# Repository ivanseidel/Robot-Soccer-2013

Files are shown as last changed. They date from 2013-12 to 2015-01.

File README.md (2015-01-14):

Soccer-Robot-2013
=================

RoboCup Junior Soccer

This repository was created to share the entire RoboCup Junior Soccer robot project,
including Rendering, SolidWorks CAD drawings, simulations, software code and libraries.

The project was developed by team EmeroCHS (Emerotecos with CHS)  from Brazil, for the national and international
RoboCup at Eidhoven.

At the same time, we were developing a Soccer B robot for RoboCup too. They both use almost the same electronics design and concept. Here is the [Rescue B project repository](https://github.com/ivanseidel/Robot-Rescue-2013).

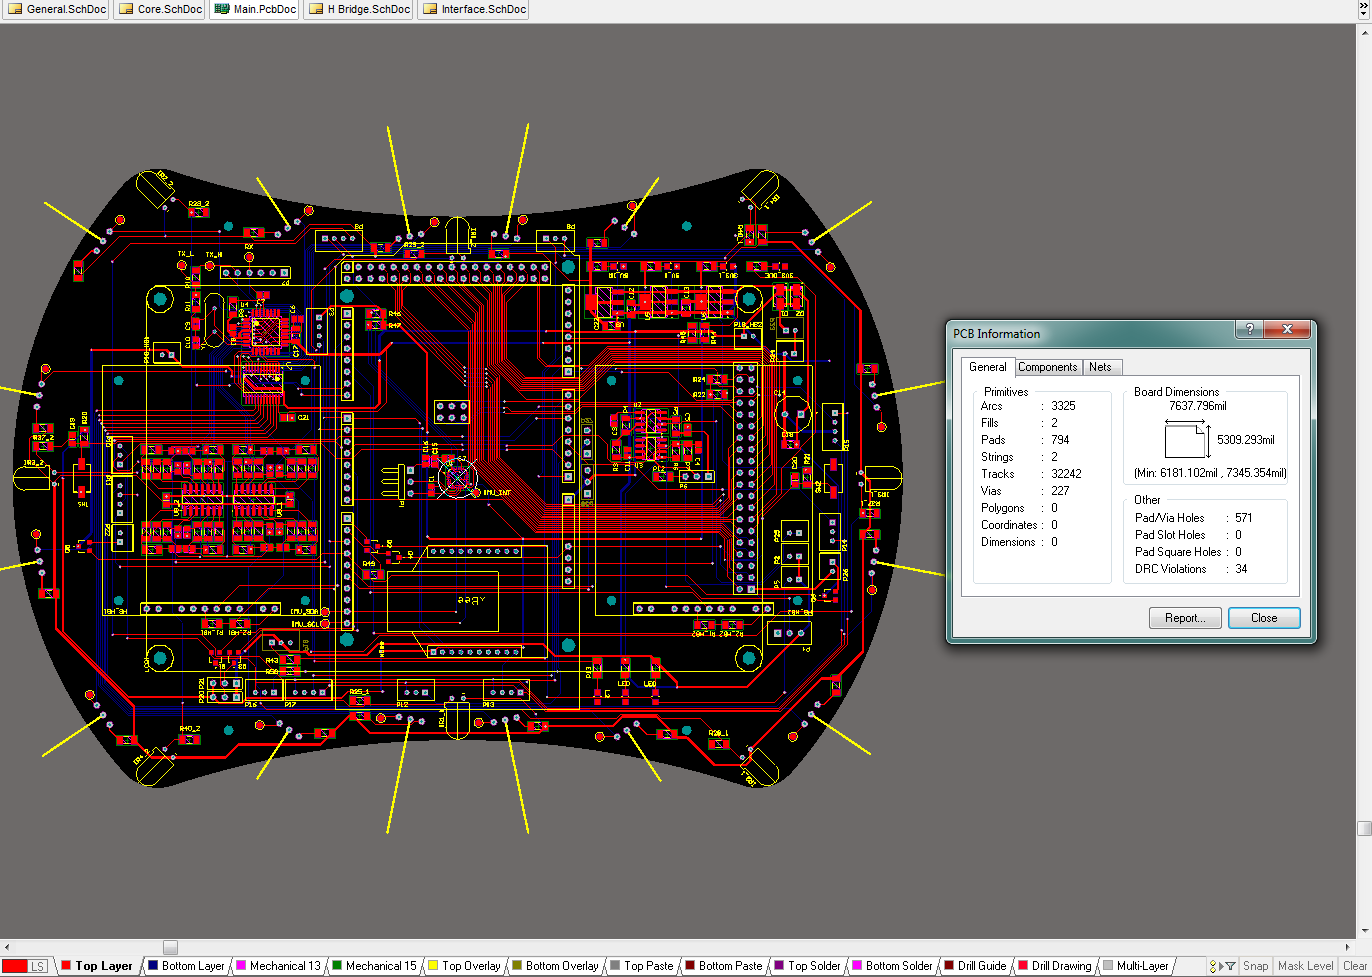
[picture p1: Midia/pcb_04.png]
RoboCup Junior Soccer Electronics

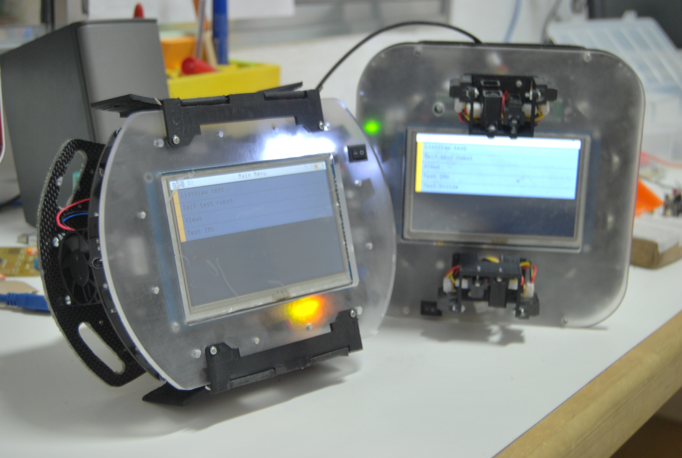
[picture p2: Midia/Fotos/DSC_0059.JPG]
RoboCup Junior Soccer Project


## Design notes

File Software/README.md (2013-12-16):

 Soccer-Robot-2013 | Software
=================

## What is included here

### Libraries
Folder containing _almost_ all libraries used by projects. Others are contained in my [repositories](https://github.com/ivanseidel).

### SlaveKalman, Slave, SlaveIntensity, SlaveFast and SlaveRequest
Different, tested versions for the "Ball location" Firmware. The actually used is SlaveKalman, witch can filter and preddict even in noisy enviroments, where the ball is. This runs on the Atmega328, at 16Mhz.

### Soccer_v01 and Soccer_v02
Actual main code. Version 2 was the last one, and the final one as well.

Includes majority of funcion, interface to connect to external hardware. Operational System setup, robot setup, bluetooth management, Sensors and motors setup and checkup.

### Tests
Code that was kept to save time, and test specif purpouse tasks.

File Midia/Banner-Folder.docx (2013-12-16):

Software:

Complete Object Oriented sofrware

Interfaced with ArduinoOS

Positioned by Kalman Filter

Eletronic:

4 – IR Distance sensor

4 – Ultrasonic Sensor

8 – Analogic IR Sensor with band pass filter

16 – IR digital sensor

1 - 9 axis IMU with Sensor Fusion Quaternion Output

1 – 5” TFT LCD 800-480 with Touch screen

1 – Serial Bluetooth - Xbee

1 – ARM Cortex M3 - 100MHz

1 – AtMega 328 - 16MHz

Mechanics:

100% - Developed on SolidWorks

4 – Designed Omnidirectional Wheels

4 – High torque motors

2 – High torque servos

4mm - Carbon Fiber with Triaxial Kevlar Chassi

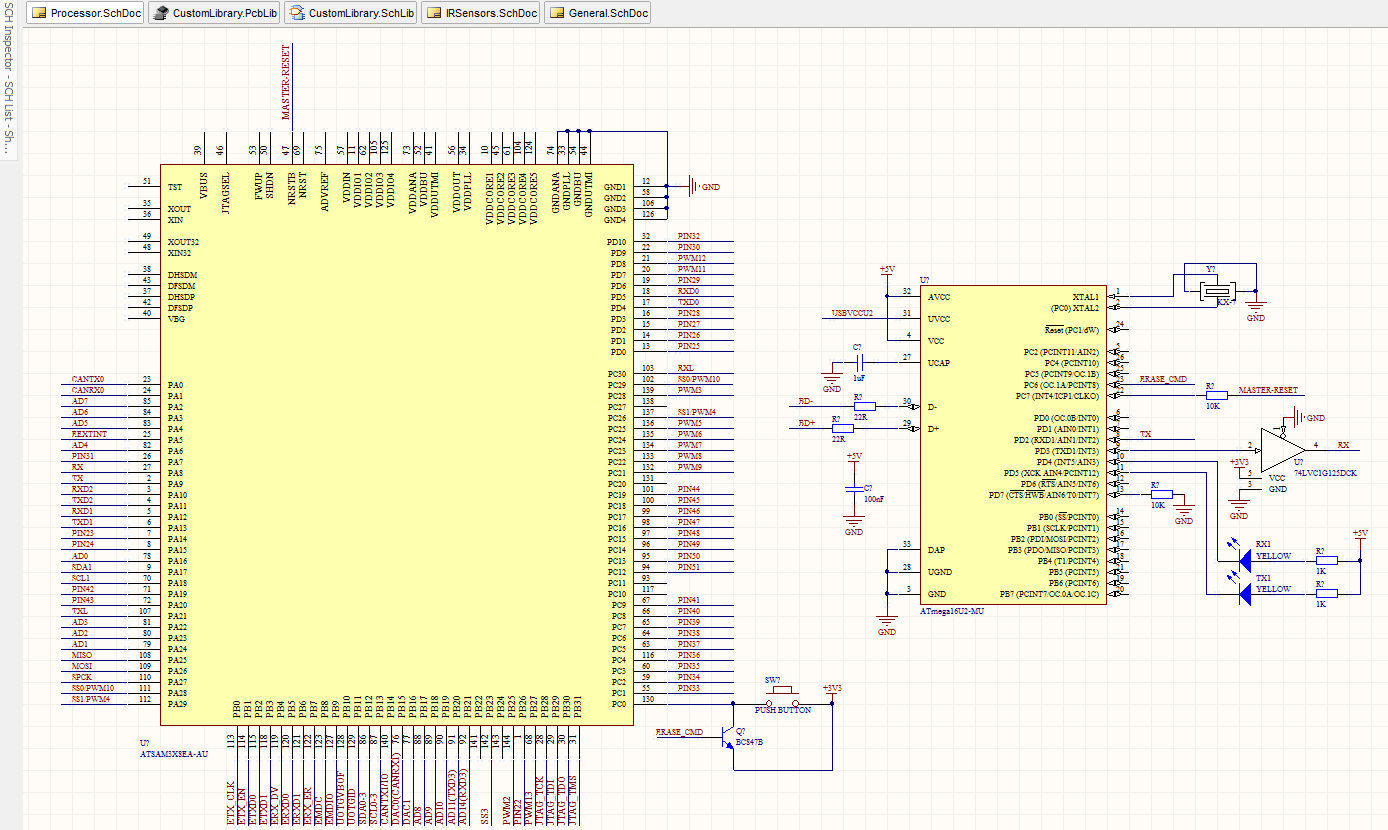
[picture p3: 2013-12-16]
Midia/schematic_01.png

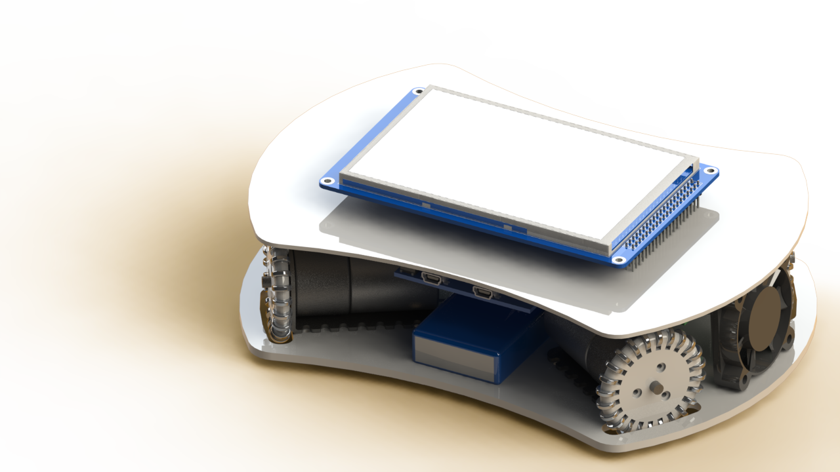
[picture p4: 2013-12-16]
Midia/robot_03.png

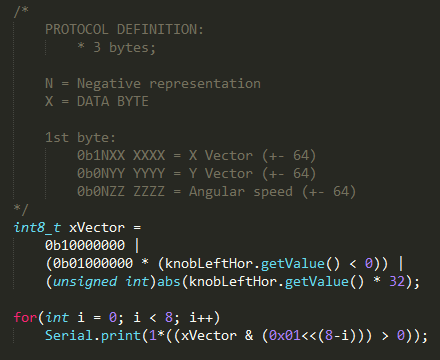
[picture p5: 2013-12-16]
Midia/code_crazy_1.png

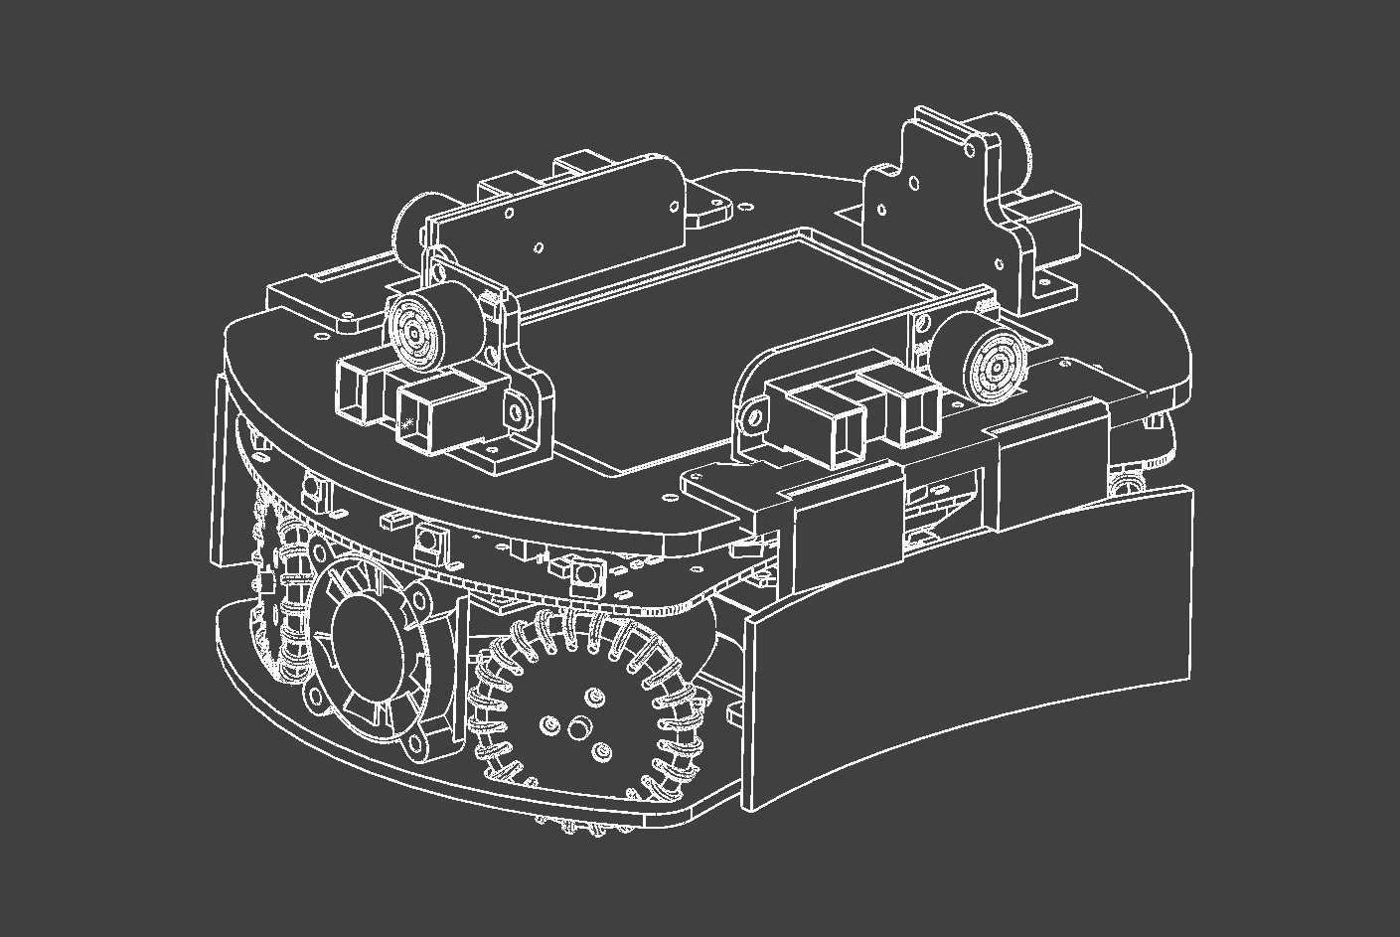
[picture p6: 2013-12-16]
Midia/robot_07.png

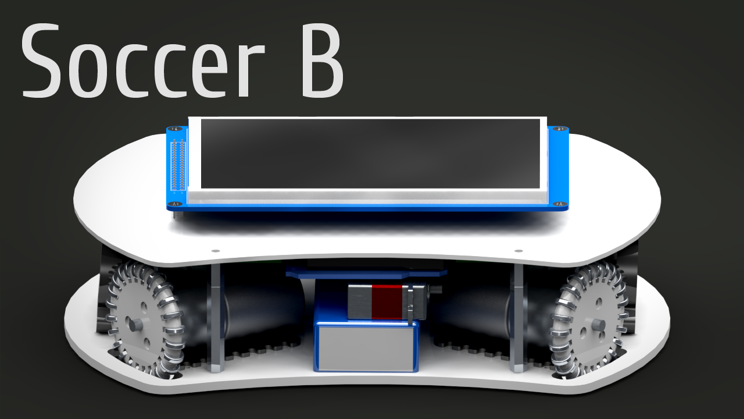
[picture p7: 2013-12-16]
Midia/info_06.png

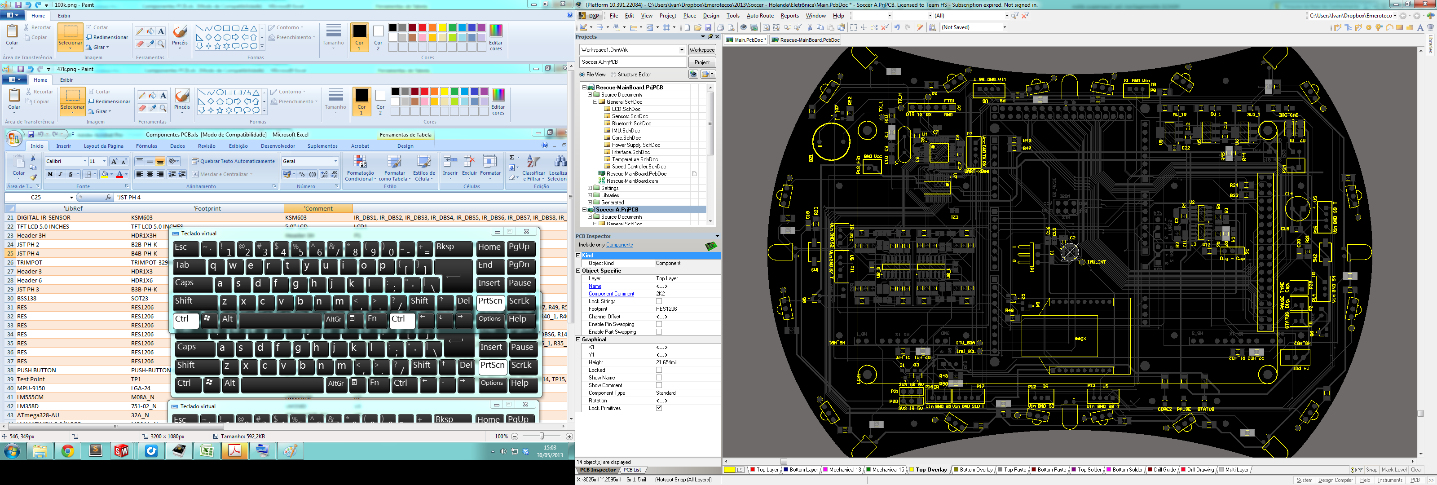
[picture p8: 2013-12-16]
Midia/2k2.png

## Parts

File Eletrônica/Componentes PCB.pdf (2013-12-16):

LED | LED0805 LED | 3V3_1, 3V3_DUE, 5V_1, 5V_IR, L1, L2, L7
BUZZER | BUZZER | Buzzer BZ1
Cap Semi | C0805 | 0.1uF | C1, C6, C7, C8, C15, C21
Cap Semi | C0805 | 2.2nF | C2
Cap Semi | C0805 | 100pF C3, C4, C5, C11
Cap Semi | C0805 | 22pF | C9, C10
Cap Semi | C1206 | 10uF | C12, C13, C17, C18, C22
94SA107X0010EE | 470uF C14
Cap Semi | C0805 | 10nF | C16
Cap Semi | 6‐0805_N 100nF C19, C20
Cap Semi | C0805 | 1nF | C23_1, C23_2, C24_1, C24_2, C27_1, C27_2, C28_1, C28_2
Cap Semi | C0805 | 1uF | C25_1, C25_2, C26_1, C26_2, C29_1, C29_2, C30_1, C30_2
Cap Semi | 6‐0805_N Cap Sem C31_1, C31_2
DIODE | DIODESMA1N4004 D1, D2
POLOLU‐QIK‐2SPOLOLU‐Q H BRIDG HB_HB1, HB_HB2
LED | LED‐5mm ‐IR | IR1_1, IR1_2, IR2_1, IR2_2, IR3_1, IR3_2, IR4_1, IR4_2
DIGITAL‐IR‐SEN KSM603 KSM603 IR_DBS1, IR_DBS2, IR_DBS3, IR_DBS4, IR_DBS5, IR_DBS6, IR_DBS7, IR_ TFT LCD 5.0 INCTFT LCD 5.05.0" LCD LCD1
Header 3H | HDR1X3H Header 3P1
JST PH 2 | B2B‐PH‐K JST PH 2 P2, P5, P18_HB1, P18_HB2, P22, P23, P24, P25, P26
JST PH 4 | B4B‐PH‐K JST PH 4 P3, P9, P11, P13, P15, P17
TRIMPOT | TRIMPOT‐310K | P4
Header 3 | HDR1X3 Header 3P6, P20, P21, P27, P28
Header 6 | HDR1X6 Header 6P7
JST PH 3 | B3B‐PH‐K JST PH 3 P8, P10, P12, P14, P16, P19
BSS138 | SOT23 | BSS138 Q1, Q2, Q3, Q4, Q5, Q6, Q7
RES | RES1206 10K | R1_HB1, R1_HB2, R5, R6, R9, R10, R12, R20, R21, R24, R43, R44, R46, R
RES | RES1206 2K2 | R2_HB1, R2_HB2, R7, R11, R25_1, R25_2, R28_1, R28_2, R37_1, R37_2
RES | RES1206 100K | R3, R4, R16_1, R16_2, R17_1, R17_2, R33_1, R33_2, R34_1, R34_2
RES | RES1206 1K | R15, R19_1, R19_2, R23_1, R23_2, R27_1, R27_2, R31, R32_1, R32_2,
RES | RES1206 10R | R22
RES | RES1206 47K | R26_1, R26_2, R29_1, R29_2, R38_1, R38_2, R41_1, R41_2
PUSH BUTTON PUSH‐BUTTPUSH BUSW1, SW2
Test Point | TP1 | Test PoinTP1, TP2, TP3, TP4, TP5, TP6, TP7, TP8, TP9, TP10, TP11, TP12, TP13, TP
MPU‐9150 | LGA‐24 | MPU‐915U1
LM555CM | M08A_N LM555CMU2
LM358D | 751‐02_N LM358D U3
ATmega328‐AU32A_N | ATmega3U4
LM1117IMPX‐5 MP04A_N LM1117IU5, U9 LM1117IMPX‐3 MP04A_N LM1117IU6
MUX‐74HC4067SSOP‐24 4067 | U7
LM224D | SO14_N | LM224D U8_1, U8_2
xBee | xBee | xBee | xBee
OSC‐2‐PIN | OSC‐2‐PIN‐16Mhz Y1

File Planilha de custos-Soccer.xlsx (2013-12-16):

 | PLANILHA DE CUSTOS - SOCCER 2013 |  |  |  |  |  | TOTAL | R$6389.48 |  | RobotShop
(w,s) |  |  |  |  |  |  | Dolar: | $2.20 |  | R$2398.09
OK | Descrição | Fornecedor | Qtd | Extra | Valor | Imposto | Dolar? | Subtotal | Link
w | Camada de proteção em acrilico | CopyExpress | 1 | 1 | 0.00 |  |  | R$0.00
w | LCD TFT 5" | Dealextreme | 2 | 1 | 54.50 |  | s | R$359.70 | http://dx.com/p/800-x-480-5-0-lcd-tft-touch-screen-module-w-stylus-pen-for-arduino-blue-154505
w | Bluetooth | Dealextreme | 2 | 0 | 11.70 |  | s | R$51.48 | http://dx.com/p/bluetooth-master-uart-board-communication-module-blue-152175
w | Capacitores 0805 | Dealextreme | 2 | 0 | 7.60 |  | s | R$33.44 | http://dx.com/p/smd-0805-capacitors-white-20-x-30-pcs-152739
w | Capacitor 1206 10uF | Dealextreme | 1 | 0 | 4.80 |  | s | R$10.56 | http://dx.com/p/avx-1206-smd-10uf-16v-type-a-tantalum-capacitors-30-pcs-148546
 | Bateria Lipo 1.6A 40C 2S 7.4v | HobbyKing | 8 | 2 | 9.49 |  | s | R$208.78 | http://www.hobbyking.com/hobbyking/store/__10278__Turnigy_2200mAh_2S_40C_Lipo_Pack.html
w | Servo motor - Ultra Fast/High Torque/3kg/.06sec/21g (Kicker) | HobbyKing | 4 | 1 | 23.94 |  | s | R$263.34 | http://hobbyking.com/hobbyking/store/uh_viewItem.asp?idProduct=24764
w | Shipping | HobbyKing | 1 | 0 | 30.00 |  | s | R$66.00
w | IMU InveSense (MPU-9150) | InveSense | 2 | 1 | 17.00 | 70% | s | R$190.74 | http://www.invensense.com/mems/gyro/mpu9150.html
w | Shipping | InveSense | 1 | 0 | 53.95 | 70% | s | R$201.77
w | Circuito Impresso - 10 unidades, 20cm x 15cm, Dupla Face, 1.6mm | Itead | 1 | 0 | 90.00 | 70% | s | R$336.60 | http://imall.iteadstudio.com/open-pcb/pcb-prototyping/im120418010.html
w | Shipping | Itead | 1 | 0 | 30.00 | 70% | s | R$112.20
 | Standoffs (? mm) FF | Pololu | 2 | 2 | 1.69 | 70% | s | R$25.28
 | Standoffs (? mm) MF | Pololu | 2 | 2 | 1.29 | 70% | s | R$19.30
 | Standoffs (? mm) MF | Pololu | 2 | 2 | 1.29 | 70% | s | R$19.30
w | Motores 25D (47:1) | Pololu | 8 | 0 | 21.95 | 70% | s | R$656.74 | http://www.pololu.com/catalog/product/2286
w | Shipping | Pololu | 1 | 0 | 46.95 | 70% | s | R$175.59
 | Driver de motor (QIK 2S12V10) | Pololu | 4 | 0 | 74.95 | 70% | s | R$1121.25 | http://www.pololu.com/catalog/product/1112
w | Bracket Motor 25D (Par) | Pololu | 4 | 1 | 7.45 | 70% | s | R$139.31 | http://www.pololu.com/catalog/product/1569
w | Capacitores, Resistores, Transistores, IC's (Patrocínio) | Proesi | 0 | 0 | 0.00 |  |  | R$0.00
w | Arduino DUE | RobotShop | 2 | 2 | 49.95 | 70% | s | R$747.25 | http://www.robotshop.com/productinfo.aspx?pc=RB-Ard-40&lang=en-US
w | Distance IR (20-150cm) | RobotShop | 8 | 2 | 14.59 | 70% | s | R$545.67 | http://www.robotshop.com/productinfo.aspx?pc=RB-Dem-02&lang=en-US
w | Shipping | RobotShop | 1 | 0 | 40.00 | 70% | s | R$149.60
 | 10pin xBee Socket | RobotShop | 4 | 2 | 1.00 | 70% | s | R$22.44 | http://www.robotshop.com/productinfo.aspx?pc=RB-Spa-631&lang=en-US
w | Maxbotix LV-MaxSonar-EZ1 (Ultra som) | RobotShop | 8 | 2 | 24.95 | 70% | s | R$933.13 | http://www.robotshop.com/maxbotix-ez1-ultrasonic-ranger-1.html

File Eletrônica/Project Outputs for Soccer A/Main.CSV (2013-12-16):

Bill of Material for
On 18/05/2013 at 18:38:28
Comment | Pattern | Quantity | Components
0.1uF | C0805 | 6 | C1, C6, C7, C8, C15, C21 | Capacitor (Semiconductor SIM Model)
100K | RES1206 | 10 | R3, R4, R16_1, R16_2, R17_1, R17_2, R33_1, R33_2, R34_1, R34_2
100nF | 6-0805_N | 2 | C19, C20 | Capacitor (Semiconductor SIM Model)
100pF | C0805 | 4 | C3, C4, C5, C11 | Capacitor (Semiconductor SIM Model)
10K | RES1206 | 16 | R1_HB1, R1_HB2, R5, R6, R9, R10, R12, R20, R21, R24, R43, R44, R46, R47, R49, R52
10K | TRIMPOT-3296W | 1 | P4
10nF | C0805 | 1 | C16 | Capacitor (Semiconductor SIM Model)
10R | RES1206 | 1 | R22
10uF | C1206 | 5 | C12, C13, C17, C18, C22 | Capacitor (Semiconductor SIM Model)
16Mhz | OSC-2-PIN-TH | 1 | Y1 | 2 pin oscilator
1K | RES1206 | 18 | R15, R19_1, R19_2, R23_1, R23_2, R27_1, R27_2, R31, R32_1, R32_2, R35_1, R35_2, R36_1, R36_2, R39_1, R39_2, R42_1, R42_2
1N4004 | DIODESMA | 2 | D1, D2
1nF | C0805 | 8 | C23_1, C23_2, C24_1, C24_2, C27_1, C27_2, C28_1, C28_2 | Capacitor (Semiconductor SIM Model)
1uF | C0805 | 8 | C25_1, C25_2, C26_1, C26_2, C29_1, C29_2, C30_1, C30_2 | Capacitor (Semiconductor SIM Model)
2.2nF | C0805 | 1 | C2 | Capacitor (Semiconductor SIM Model)
22pF | C0805 | 2 | C9, C10 | Capacitor (Semiconductor SIM Model)
2K2 | RES1206 | 14 | R2_HB1, R2_HB2, R7, R11, R25_1, R25_2, R28_1, R28_2, R37_1, R37_2, R40_1, R40_2, R45, R50
330R | RES1206 | 21 | R8, R13, R14_DBS1, R14_DBS2, R14_DBS3, R14_DBS4, R14_DBS5, R14_DBS6, R14_DBS7, R14_DBS8, R14_DBS9, R14_DBS10, R14_DBS11, R14_DBS12, R14_DBS13, R14_DBS14, R14_DBS15, R14_DBS16, R18, R30, R48
4067 | SSOP-24 | 1 | U7 | MUX-74HC4067
470uF | E | 1 | C14 | Solid Aluminum Capacitor with Organic Semiconductor Electrolyte: 100uF, 10V, Bulk Pack
47K | RES1206 | 8 | R26_1, R26_2, R29_1, R29_2, R38_1, R38_2, R41_1, R41_2
5.0 LCD" | TFT LCD 5.0 INCHES | 1 | LCD1
ARDUINO DUE | ARDUINO-DUE | 1 | *
ATmega328-AU | 32A_N | 1 | U4 | 8-bit AVR Microcontroller, 32KB Flash, 1KB EEPROM, 2KB SRAM, 32-pin TQFP, Industrial Grade (-40°C to 85°C)
BSS138 | SOT23 | 7 | Q1, Q2, Q3, Q4, Q5, Q6, Q7 | N-Channel Enhancement Mode Vertical DMOS FET
Buzzer | BUZZER | 1 | BZ1 | Buzzer
Cap Semi | 6-0805_N | 2 | C31_1, C31_2 | Capacitor (Semiconductor SIM Model)
H BRIDGE | POLOLU-QIK-2S12V10-BOTTOM | 2 | HB_HB1, HB_HB2 | POLOLU QIK 2S12V10 DUAL H BRIDGE
Header 3 | HDR1X3 | 5 | P6, P20, P21, P27, P28 | Header, 3-Pin
Header 3H | HDR1X3H | 1 | P1 | Header, 3-Pin, Right Angle
Header 6 | HDR1X6 | 1 | P7 | Header, 6-Pin
IR | LED-5mm - Horizontal | 8 | IR1_1, IR1_2, IR2_1, IR2_2, IR3_1, IR3_2, IR4_1, IR4_2
JST PH 2 | B2B-PH-K | 9 | P2, P5, P18_HB1, P18_HB2, P22, P23, P24, P25, P26
JST PH 3 | B3B-PH-K | 6 | P8, P10, P12, P14, P16, P19
JST PH 4 | B4B-PH-K | 6 | P3, P9, P11, P13, P15, P17
KSM603 | KSM603 | 16 | IR_DBS1, IR_DBS2, IR_DBS3, IR_DBS4, IR_DBS5, IR_DBS6, IR_DBS7, IR_DBS8, IR_DBS9, IR_DBS10, IR_DBS11, IR_DBS12, IR_DBS13, IR_DBS14, IR_DBS15, IR_DBS16 | Generic Infra Red Sensor
LED | LED0805 | 7 | 3V3_1, 3V3_DUE, 5V_1, 5V_IR, L1, L2, L7
LM1117IMPX-3.3/NOPB | MP04A_N | 1 | U6 | 800mA Low-Dropout Linear Regulator, 4-pin SOT-223, Pb-Free
LM1117IMPX-5.0/NOPB | MP04A_N | 2 | U5, U9 | 800mA Low-Dropout Linear Regulator, 4-pin SOT-223, Pb-Free
LM224D | SO14_N | 2 | U8_1, U8_2 | Low-Power Quad Operational Amplifier
LM358D | 751-02_N | 1 | U3 | Dual Low-Power Operational Amplifier
LM555CM | M08A_N | 1 | U2 | Timer, 8-pin Narrow SOIC
MPU-9150 | QFN50P400X400X100-24N | 1 | U1 | InveSense MPU-9150 IMU 9 axles
PUSH BUTTON | PUSH-BUTTON 5,2X1,6MM | 2 | SW1, SW2
Test Point | TP1 | 16 | TP1, TP2, TP3, TP4, TP5, TP6, TP7, TP8, TP9, TP10, TP11, TP12, TP13, TP14, TP15, TP16 | Test Point for Osciloscope measurements
xBee | xBee | 1 | xBee

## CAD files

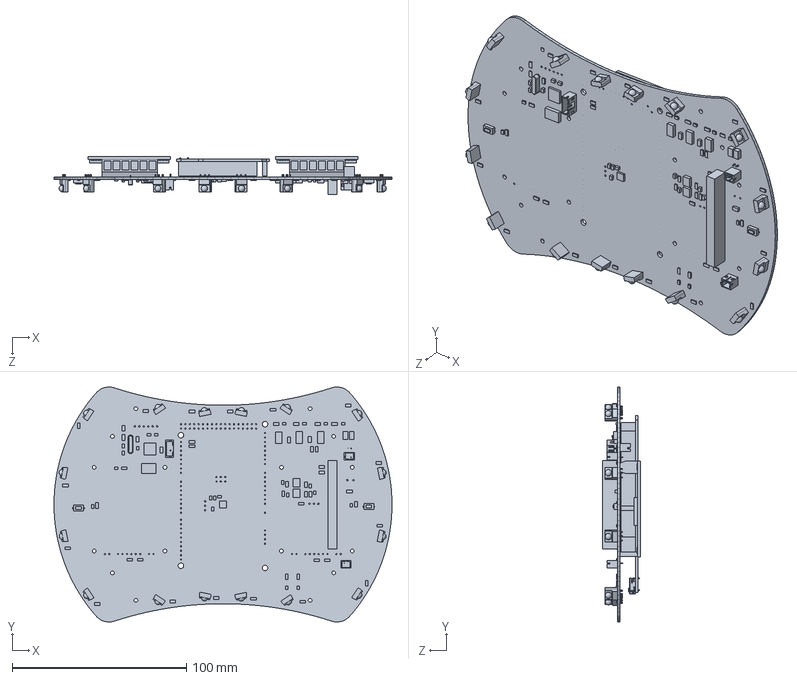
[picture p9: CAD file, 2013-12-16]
Eletrônica/Export/Main.SLDPRT
194.0 x 134.9 x 21.6 mm

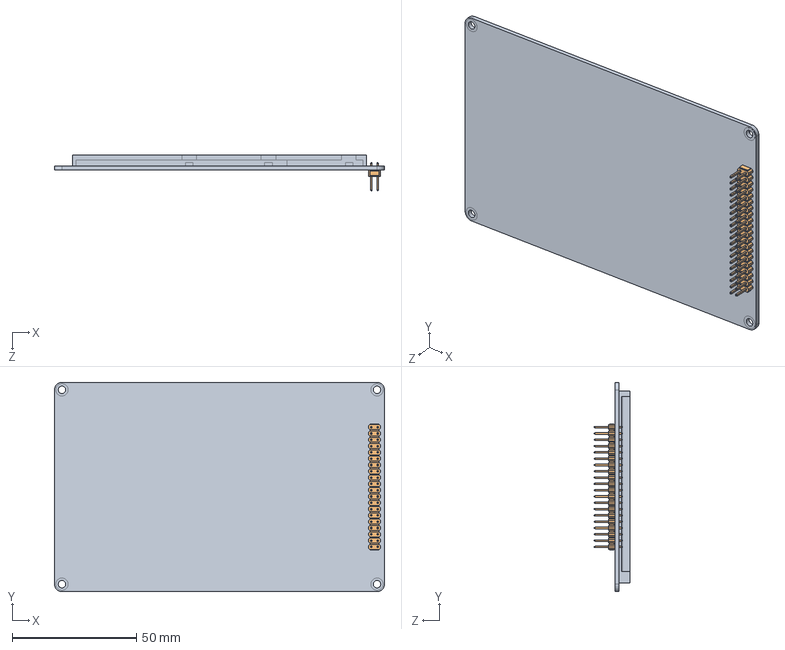
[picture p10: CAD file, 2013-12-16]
Mecânica/Eletrônica/TFT 5.0 touch screen.SLDASM
133.0 x 84.3 x 14.4 mm
TFT 5.0 touch screen
User Library-TFT 3.2 with touch screen_User Library-PLD-40

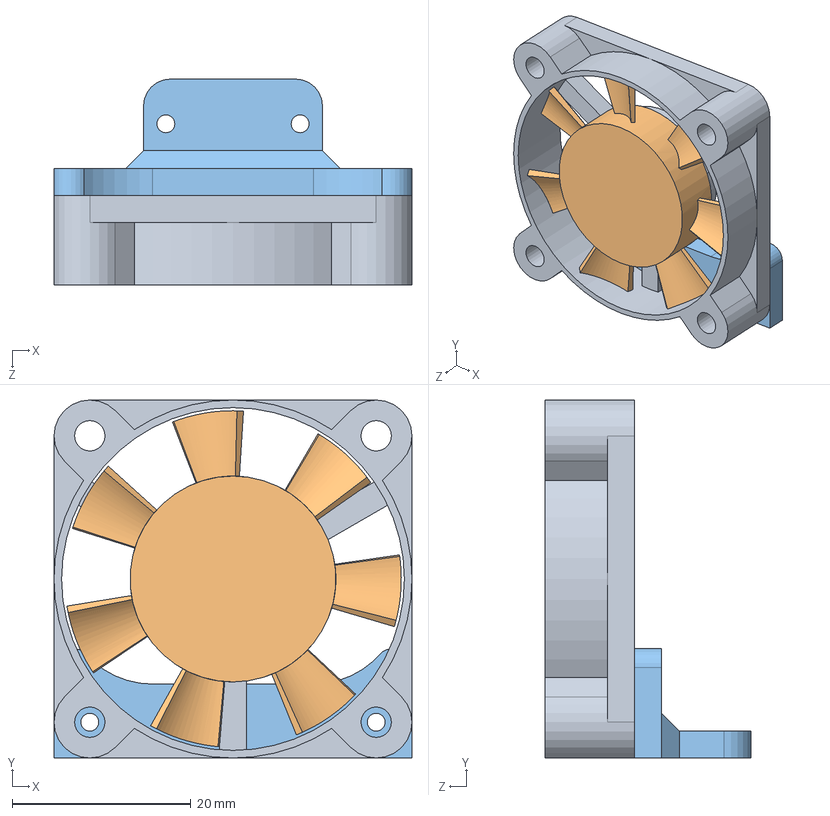
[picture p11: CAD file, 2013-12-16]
Mecânica/maker/Montagem1.SLDASM
40.0 x 40.0 x 23.0 mm
Fan-House-40x40x10-Promoco
Fan-40x40x10-Promoco
Peça1^Montagem1

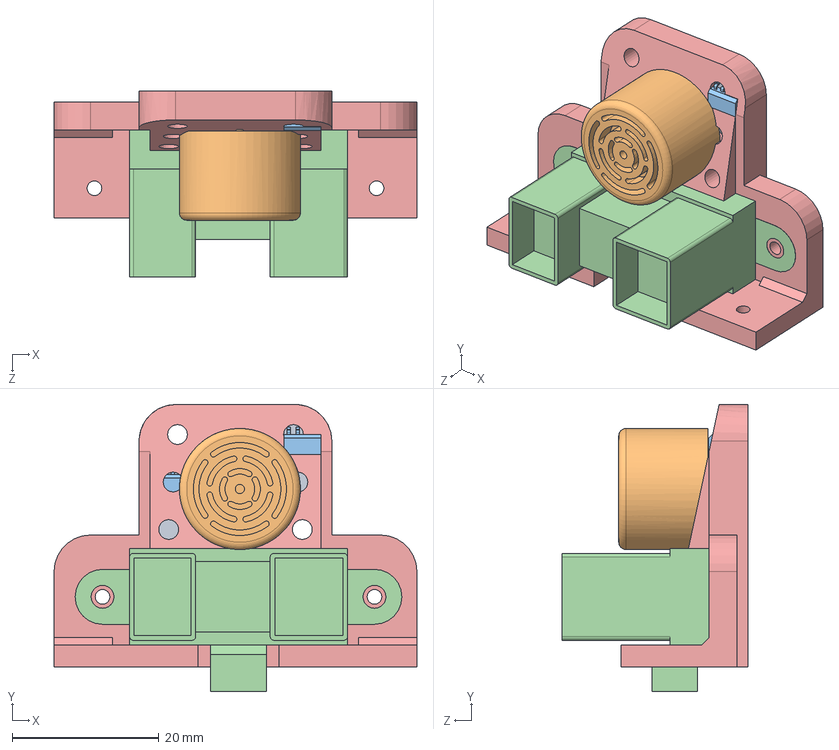
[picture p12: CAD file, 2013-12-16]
Mecânica/sensores/suporte.infravermelho-ultrasom/montagem2.SLDASM
49.5 x 39.2 x 25.3 mm
User Library-LV-MaxSonar_LV-Maxsonar PCB
User Library-LV-MaxSonar_Maxsonar Transducer
User Library-LV-MaxSonar_8 Pin SMT x 2
User Library-IR sensor-1
montegemsensores

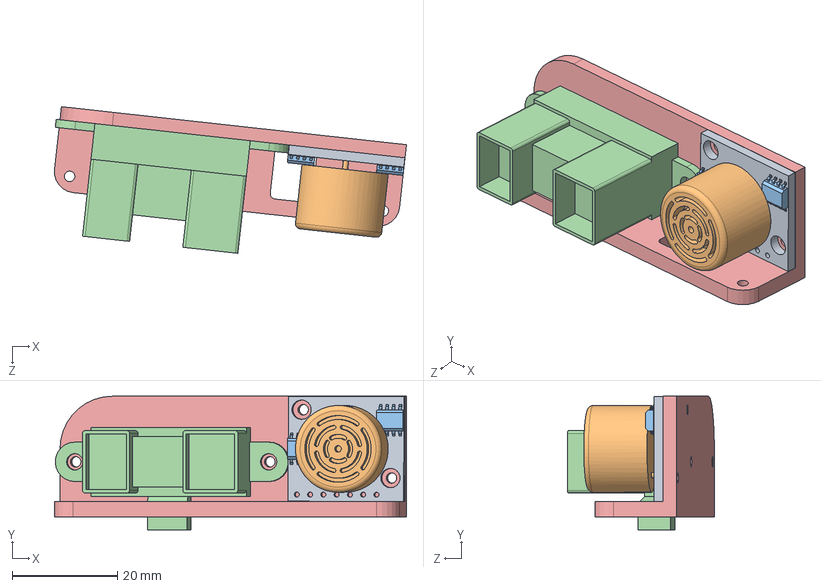
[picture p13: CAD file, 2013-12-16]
Mecânica/sensores/suporte.infravermelho-ultrasom/Montagem modificada.SLDASM
66.9 x 25.4 x 27.9 mm
User Library-LV-MaxSonar_LV-Maxsonar PCB
User Library-LV-MaxSonar_Maxsonar Transducer
User Library-LV-MaxSonar_8 Pin SMT x 2
User Library-IR sensor-1
suporte_sensores_frontal

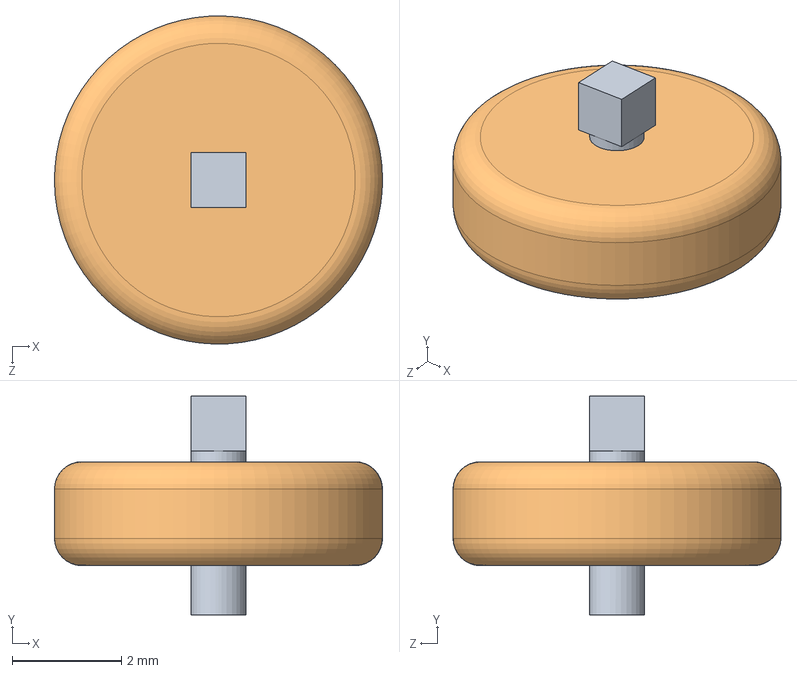
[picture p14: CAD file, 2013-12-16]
Mecânica/OmniWheel/MiniWheel.SLDASM
6.00 x 4.00 x 6.00 mm
Pino
MiniWheel

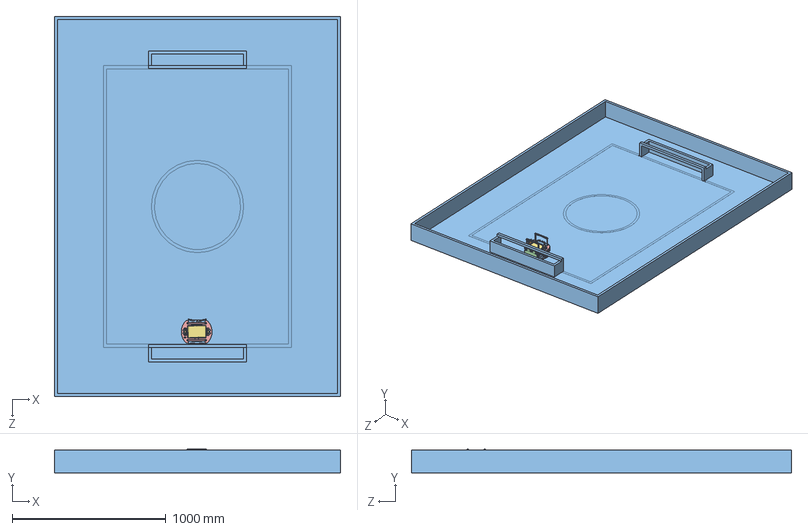
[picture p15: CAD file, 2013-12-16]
Mecânica/Geral.SLDASM
1860.0 x 154.7 x 2470.0 mm
Base
Top LCD
Pino x 96
MiniWheel x 96
Armadura x 8
Suporte_Motor-Pololu x 4
Motor x 4
Motor_Redutor x 4
Encoder x 4
Board
Ponte_H x 2
Extruded x 2
User_Library-XBee-Chip_XBee-10pin-male_1 x 2
User_Library-XBee-Chip_XBee-Chip_1
User_Library-XBee-Chip_XBee-Chip-antenna_1
Extruded_2 x 2
TFT_5.0_touch_screen_Défaut
User_Library-TFT_3.2_with_touch_screen_User_Library-PLD-40_PLD-40
Extruded_6
User_Library-Arduino_Mega_Arduino_mega_PCB
User_Library-Arduino_Mega_Header_Vertical_2_54mm_Pitch4-1_2_Way x 3
User_Library-Arduino_Mega_Atmega1280_(WGL)
User_Library-Arduino_Mega_PIN_HEADER_FEMALE_6
User_Library-Arduino_Mega_PIN_HEADER_FEMALE_8 x 5
User_Library-Arduino_Mega_PIN_HEADER_FEMALE_2X18SLDPRT
User_Library-Arduino_Mega_tactile_BUTTON
User_Library-USB_mini_B_____________ x 2
Extruded_8
Standoff-MF-30mm
Standoff-MF-13mm x 2
Standoff-FF-9mm
suporte.bateria.servo2 x 2
Servo-Turnigy-TGY-306G x 2
Bateria-Lipo2
Peça2-servo x 2
roldana direita x 2
suporte-chutador x 2
Suporte_Coller
User Library-LV-MaxSonar_LV-Maxsonar PCB x 3
User Library-LV-MaxSonar_Maxsonar Transducer x 3
User Library-LV-MaxSonar_8 Pin SMT x 6
User Library-IR sensor-1 x 3
montegemsensores x 2
suporte_sensores_frontal
Standoff - Alca x 4
alça x 2

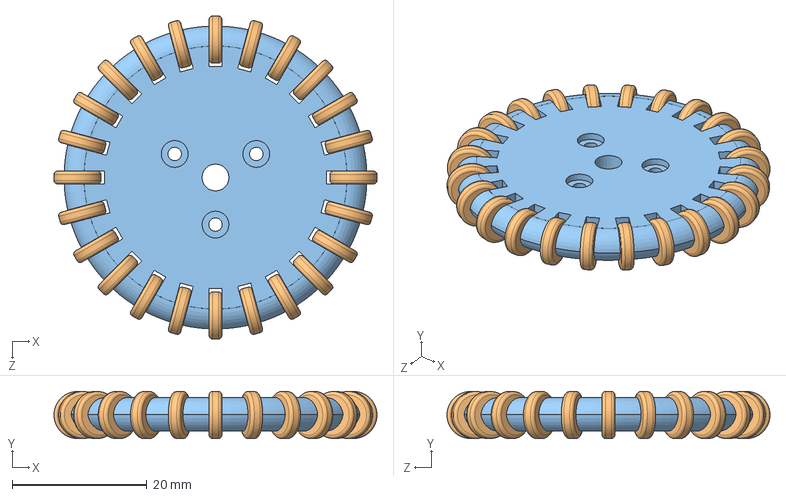
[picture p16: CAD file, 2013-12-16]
Mecânica/OmniWheel/Omniwheel.SLDASM
48.0 x 7.00 x 48.0 mm
Pino x 24
MiniWheel x 24
Armadura x 2

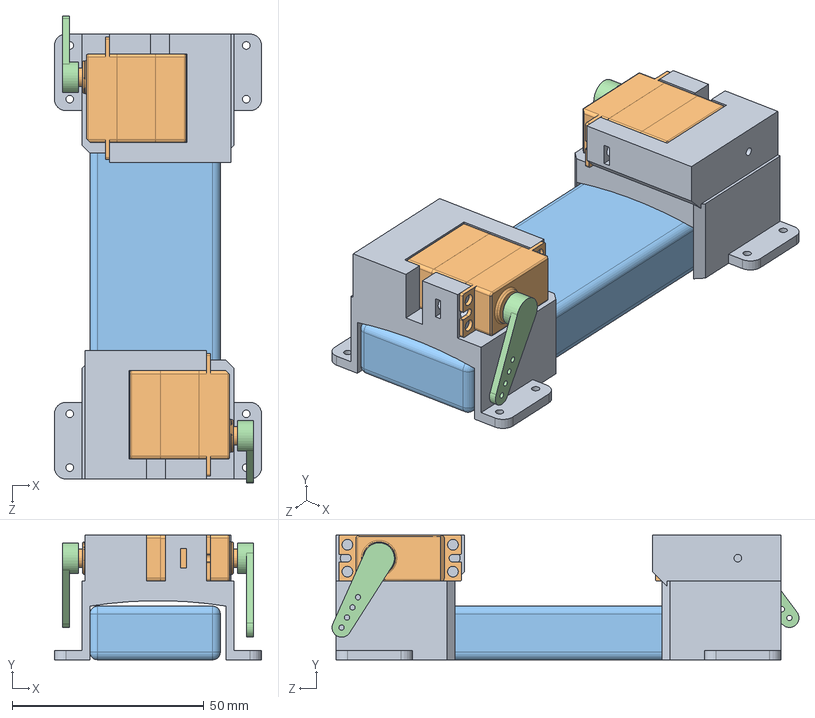
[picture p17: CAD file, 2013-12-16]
Mecânica/chutar/uniao.servo.suporte2.SLDASM
54.0 x 32.5 x 121.7 mm
suporte.bateria.servo x 2
Servo-Turnigy-TGY-306G x 2
Bateria-Lipo2
Peça1-servo x 2

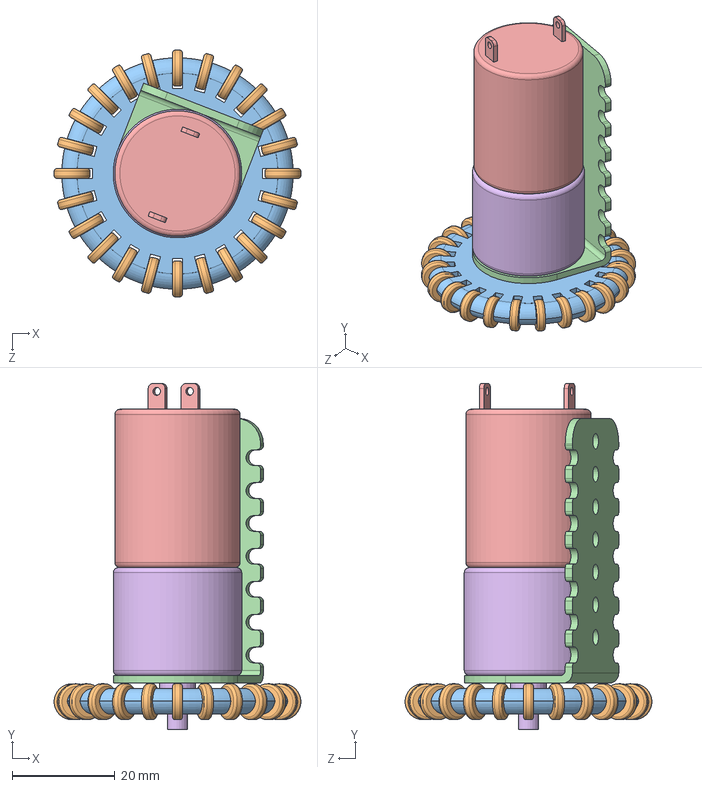
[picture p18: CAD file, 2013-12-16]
Mecânica/Partes/Montagem_Motor-Omni (ivan seidel's conflicted copy 2013-04-23).SLDASM
48.0 x 67.3 x 48.0 mm
Pino x 24
MiniWheel x 24
Armadura x 2
Suporte_Motor-Pololu
Motor
Motor_Redutor

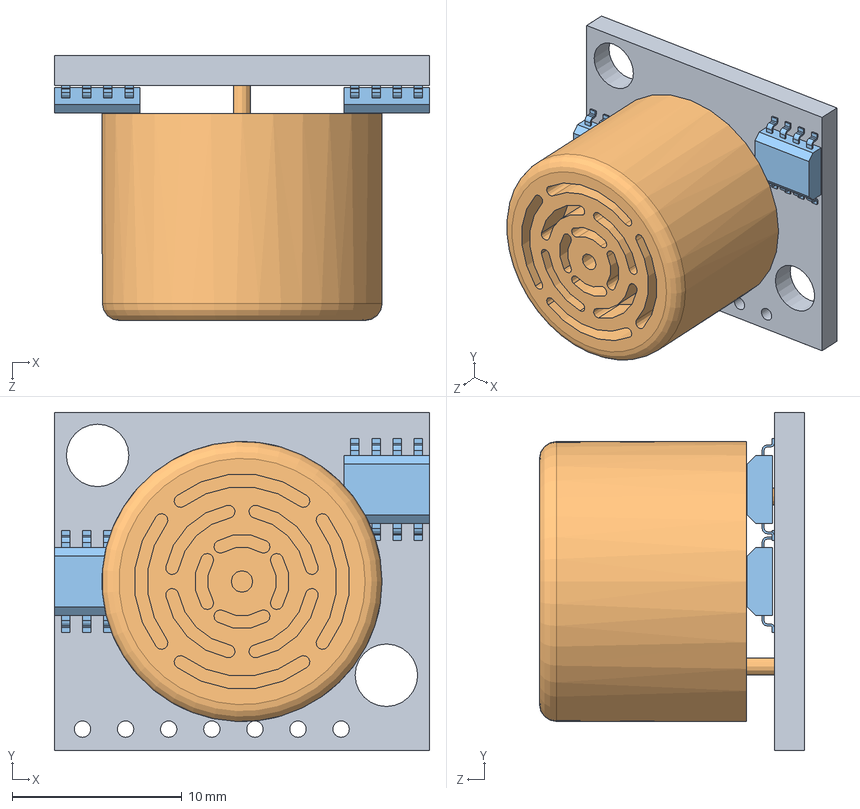
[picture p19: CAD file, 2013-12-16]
Mecânica/sensores/suporte.infravermelho-ultrasom/User Library-LV-MaxSonar.SLDASM
22.1 x 19.9 x 15.6 mm
User Library-LV-MaxSonar_LV-Maxsonar PCB
User Library-LV-MaxSonar_Maxsonar Transducer
User Library-LV-MaxSonar_8 Pin SMT x 2

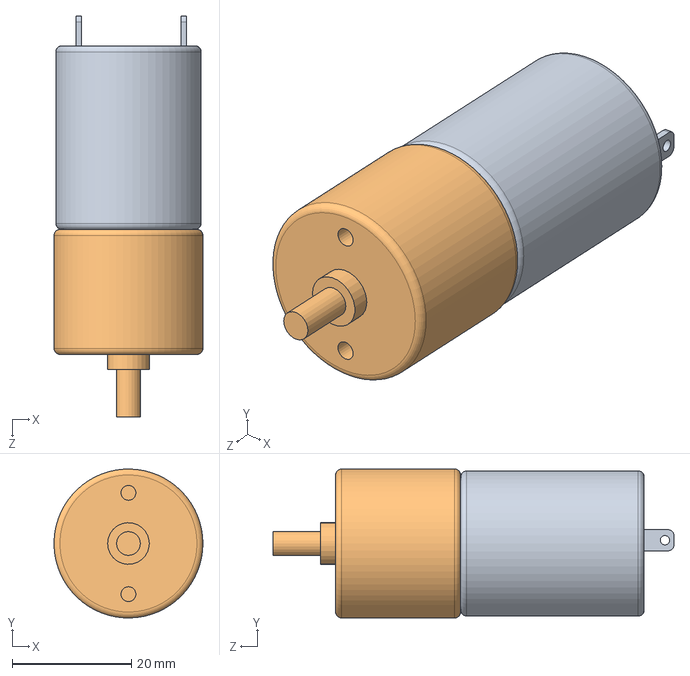
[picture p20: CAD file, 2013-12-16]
Mecânica/Partes/Motor.SLDASM
25.0 x 25.0 x 67.3 mm
Motor
Motor_Redutor

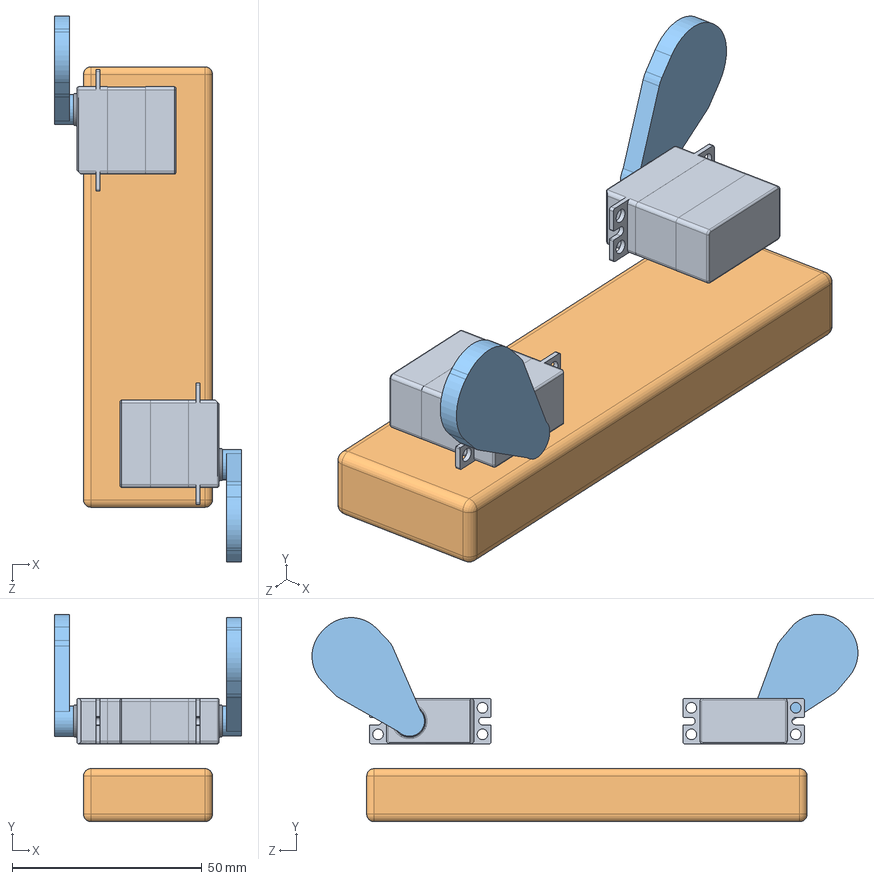
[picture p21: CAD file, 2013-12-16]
Mecânica/chutar/uniao.servo.suporte.SLDASM
49.3 x 54.6 x 143.8 mm
Servo-Turnigy-TGY-306G x 2
Bateria-Lipo2
Peça2-servo x 2

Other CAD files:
Mecânica/Eletrônica/ARDUINO_DUE.sldasm
Mecânica/Eletrônica/HB1_H_BRIDGE_2.sldasm
Mecânica/Eletrônica/xBee_2.sldasm
Mecânica/Eletrônica/HB1_H_BRIDGE_1.sldasm
Mecânica/Partes/Montagem_Motor-Omni.SLDASM
Eletrônica/Export/367500304.sldasm
Eletrônica/STEP/Ponte H.STEP
Eletrônica/STEP/Potenciometro Vertical.step
Eletrônica/STEP/Sensor-IR.STEP
Eletrônica/STEP/User Library-Arduino Mega.STEP
Eletrônica/STEP/XTAL2.step
Eletrônica/STEP/xBee.STEP
Mecânica/Alça/Standoff - Alca.SLDPRT
Mecânica/Alça/alça.SLDPRT
Mecânica/Base.SLDPRT
Mecânica/Board.sldprt
Mecânica/Diversos/Campo.SLDPRT
Mecânica/Eletrônica/367520784.sldasm
Mecânica/Eletrônica/367523728.sldasm
Mecânica/Eletrônica/408527984.sldasm
Mecânica/Eletrônica/522332160.sldasm
Mecânica/Eletrônica/Bateria-Lipo1.SLDPRT
Mecânica/Eletrônica/Bateria-Lipo2.SLDPRT
Mecânica/Eletrônica/Board.sldprt
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

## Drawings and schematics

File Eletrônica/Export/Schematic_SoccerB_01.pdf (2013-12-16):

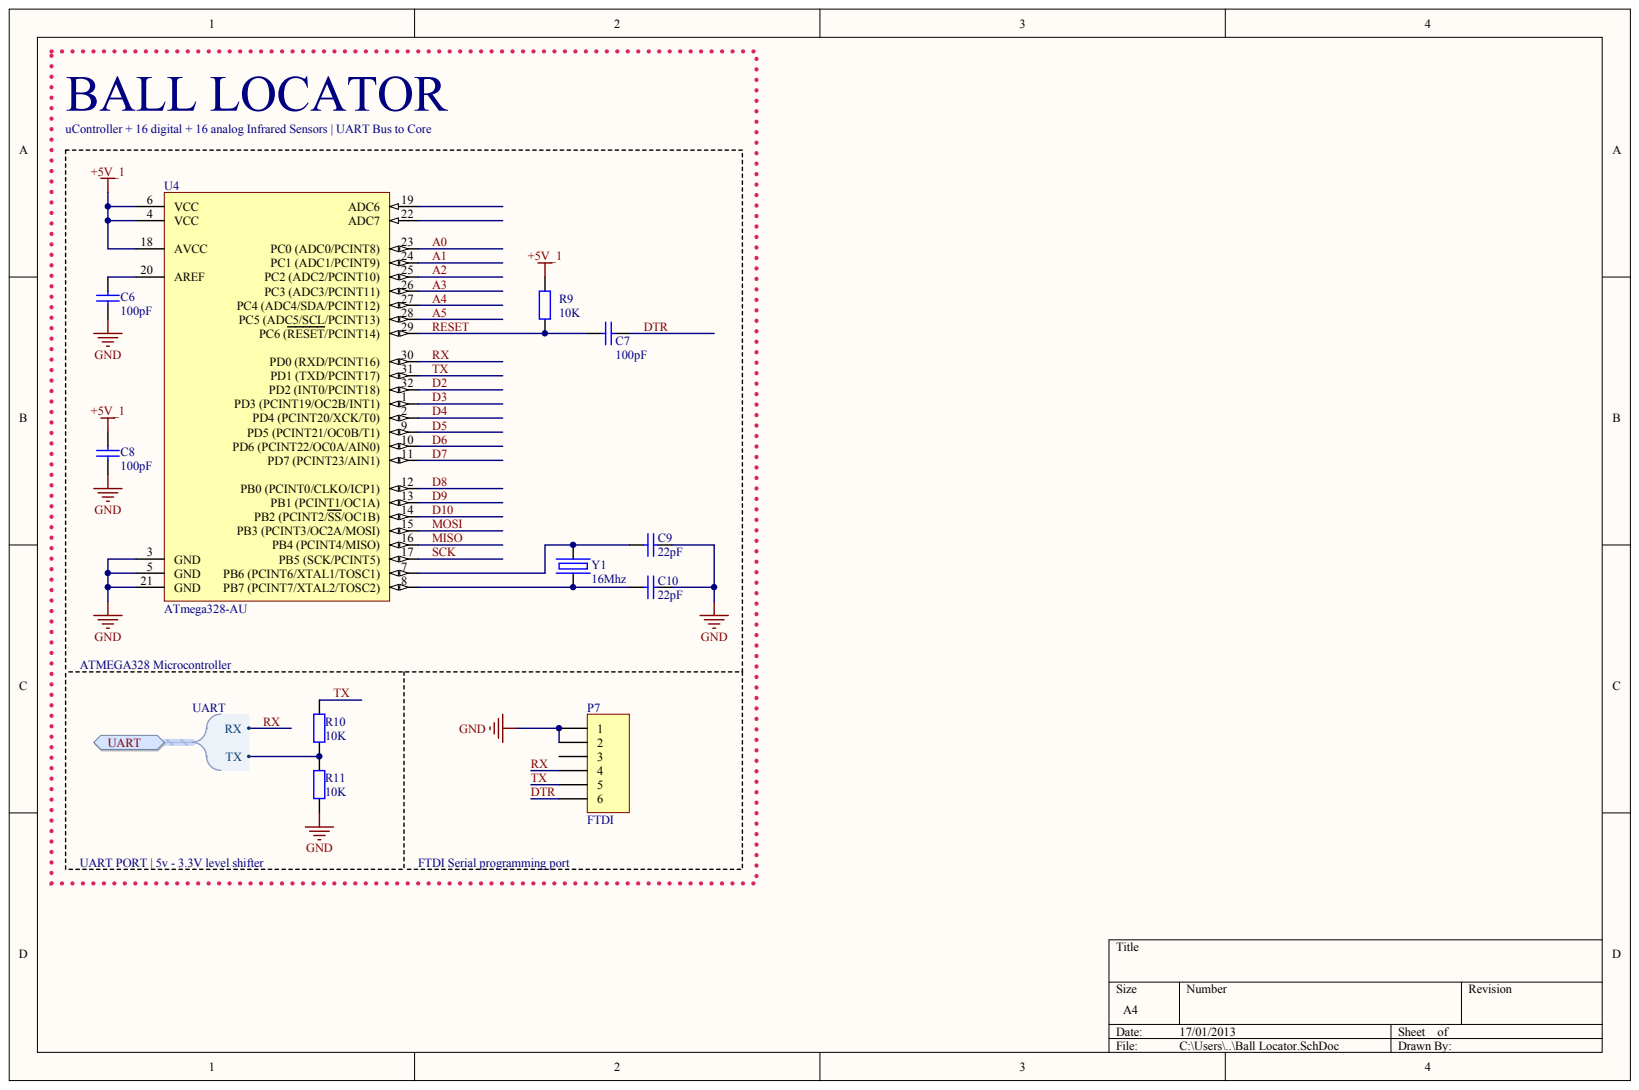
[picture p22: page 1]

uController + 16 digital + 16 analog Infrared Sensors | UART Bus to Core ATMEGA328 Microcontroller

GND 21 | 8 | 16Mhz

UART PORT | 5v - 3.3V level shift

FTDI Serial programming port

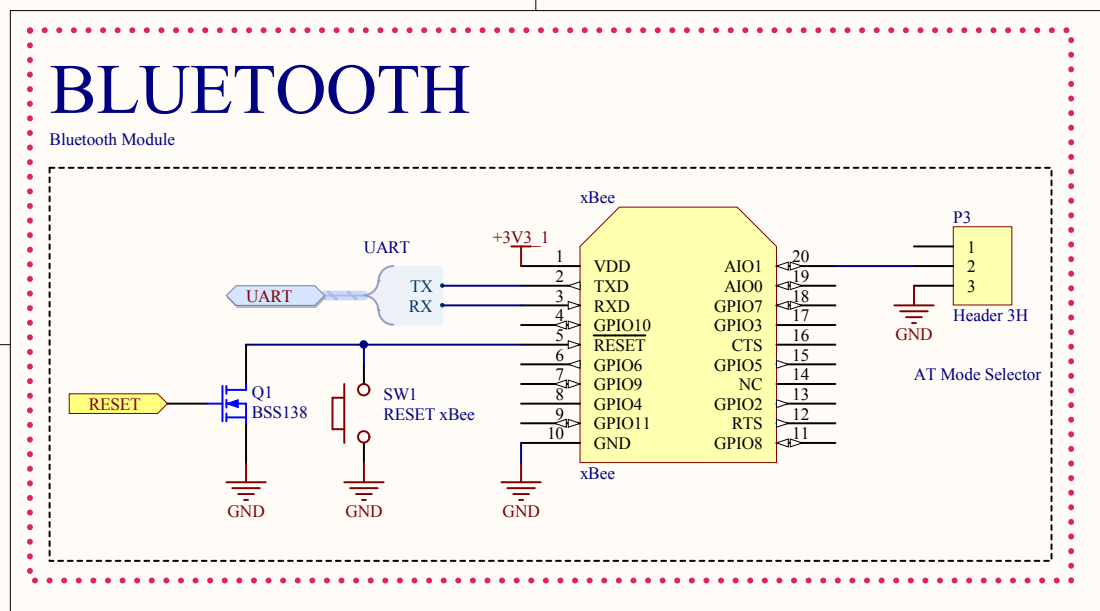
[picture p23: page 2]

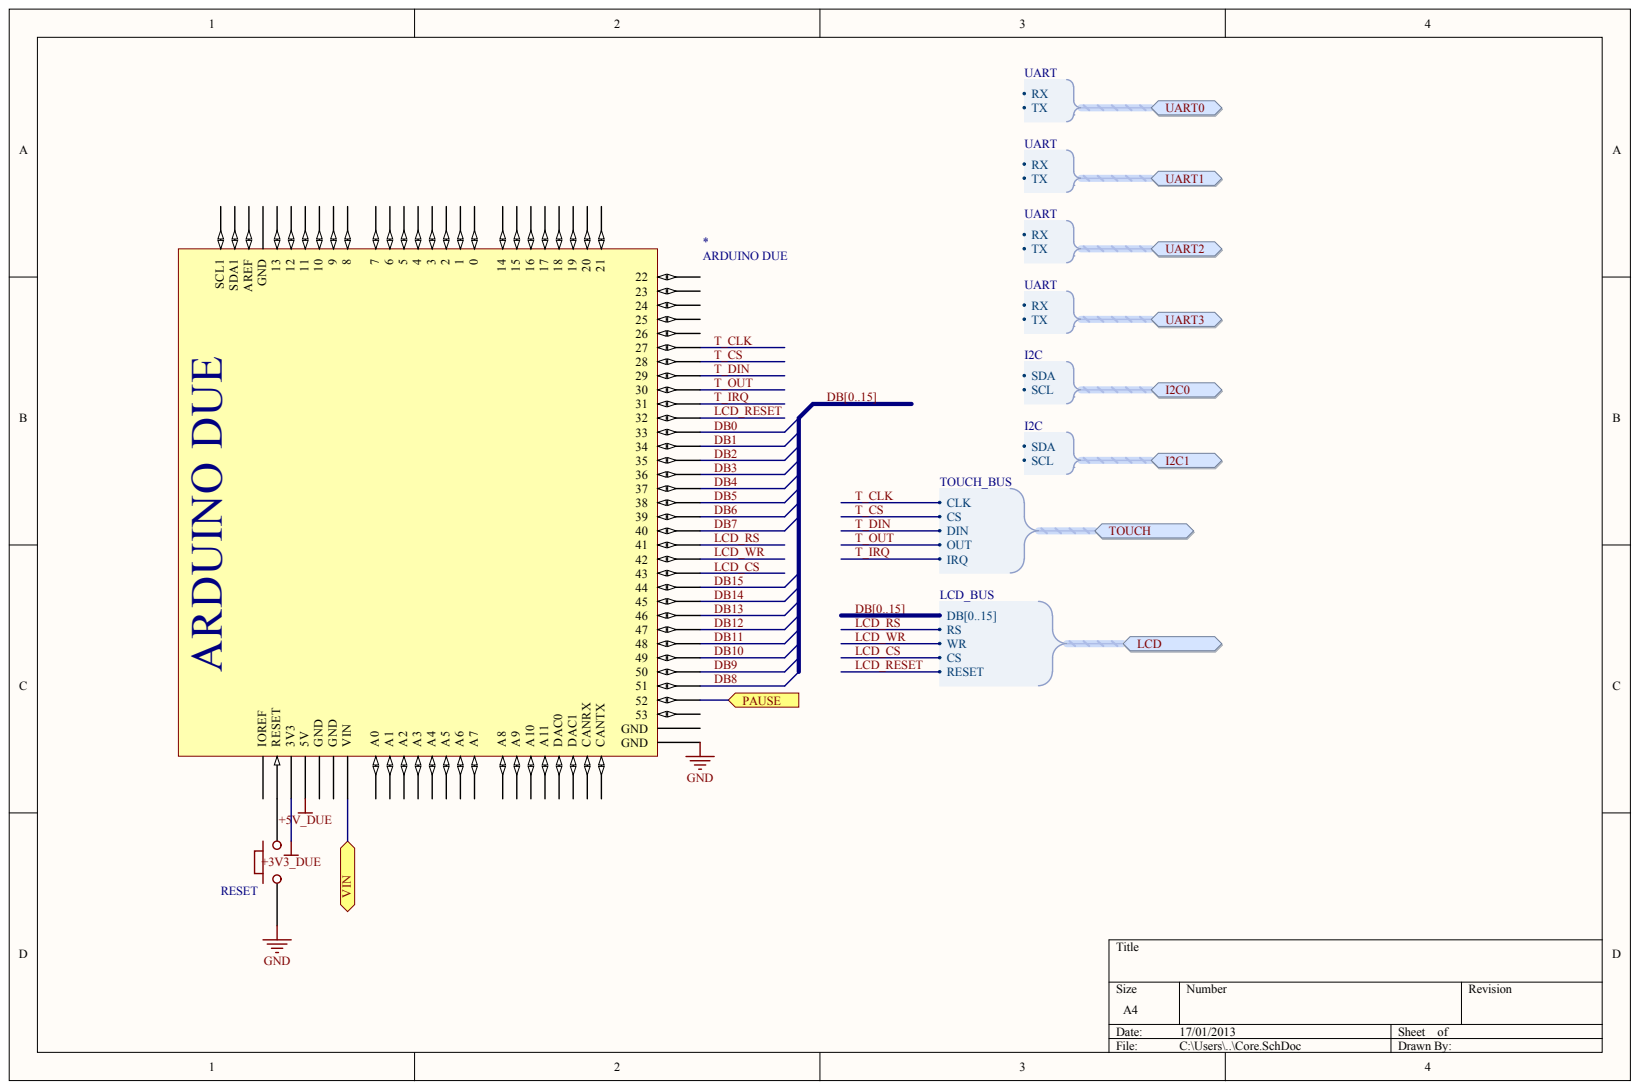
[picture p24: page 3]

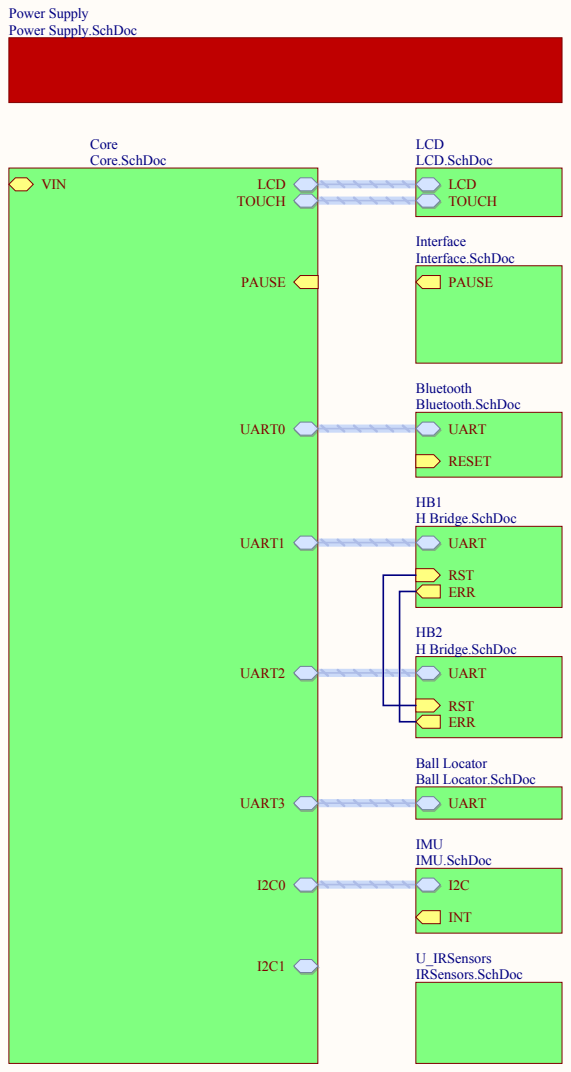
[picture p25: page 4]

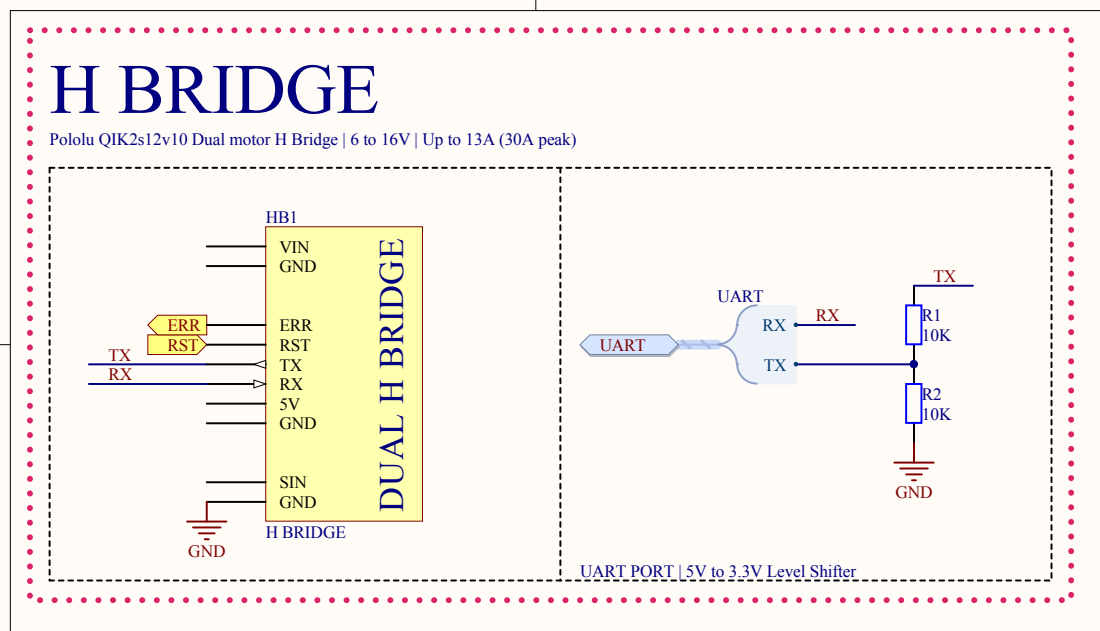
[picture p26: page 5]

Pololu QIK2s12v10 Dual motor H Bri

UART PORT | 5V to 3.3V Level Shifter

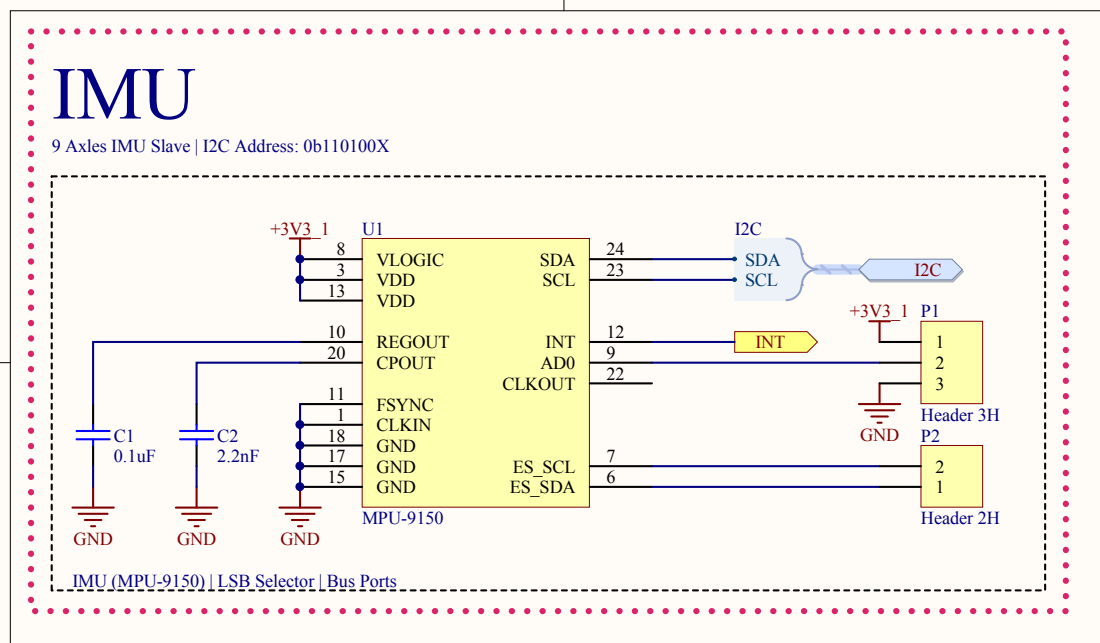
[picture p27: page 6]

U 9 Axles IMU Slave | I2C Address: 0b110100X

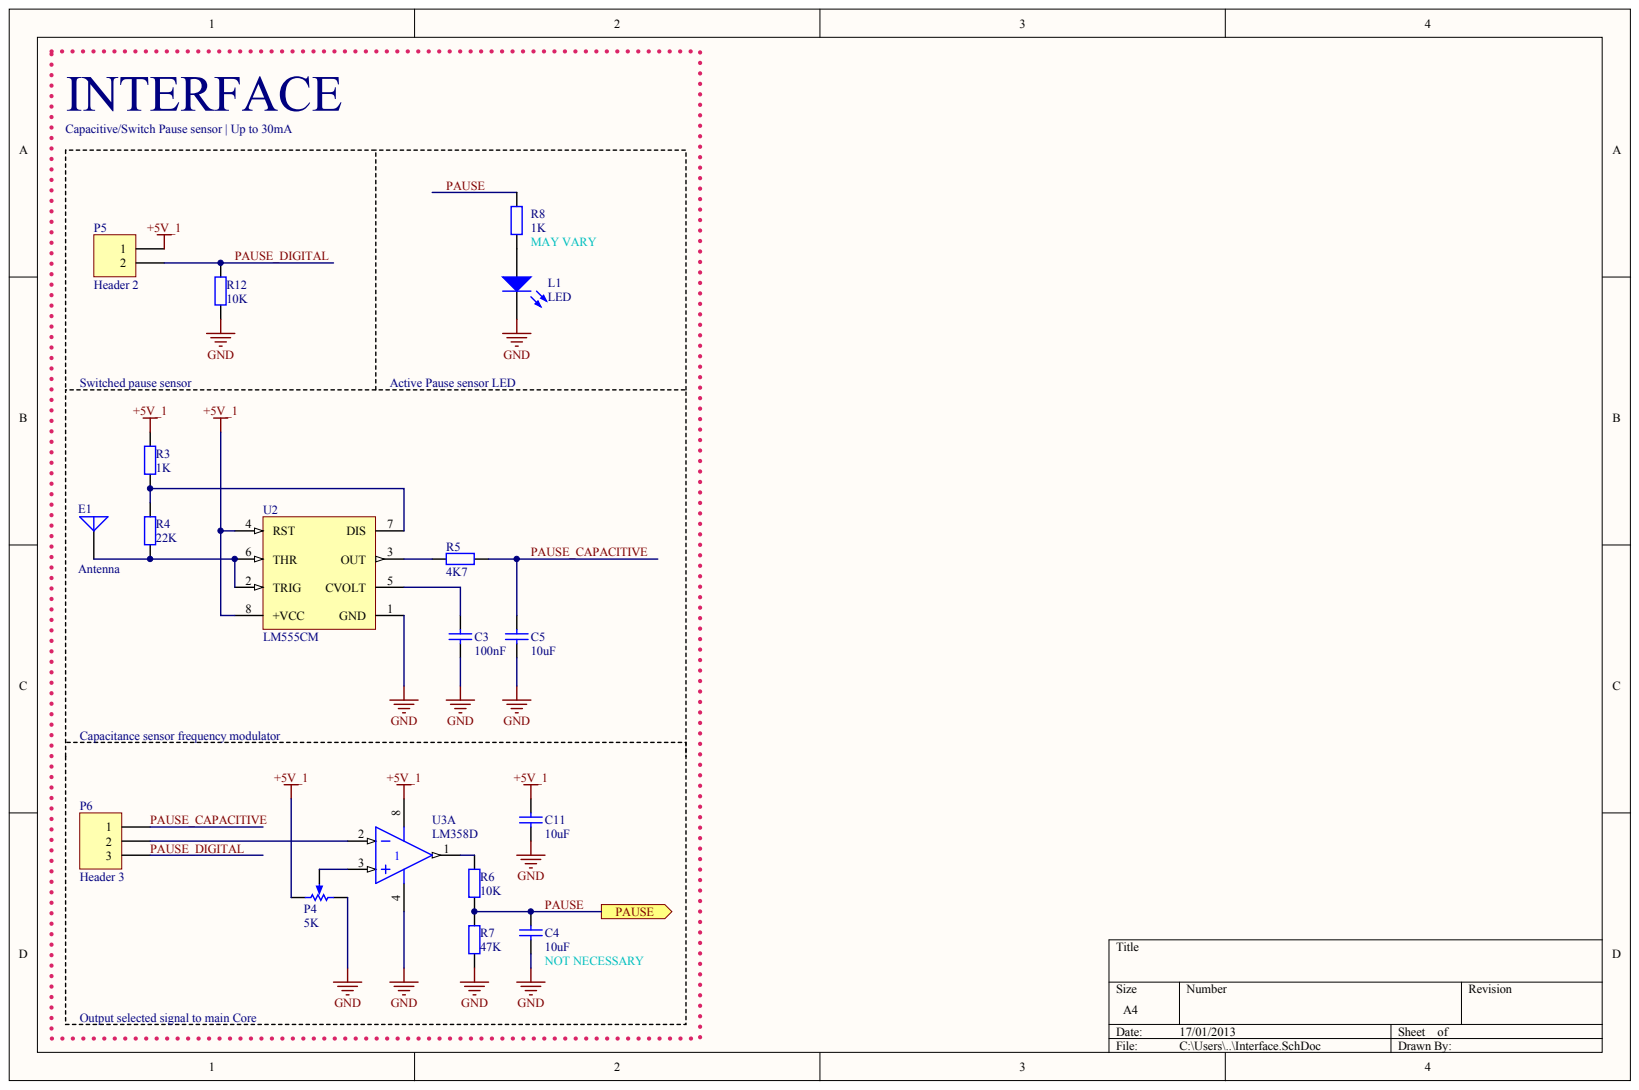
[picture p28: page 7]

Capacitive/Switch Pause sensor | Up to 30mA

Capacitance sensor frequency modulator

PAUSE_DIGITAL | 3

Output selected signal to main Core

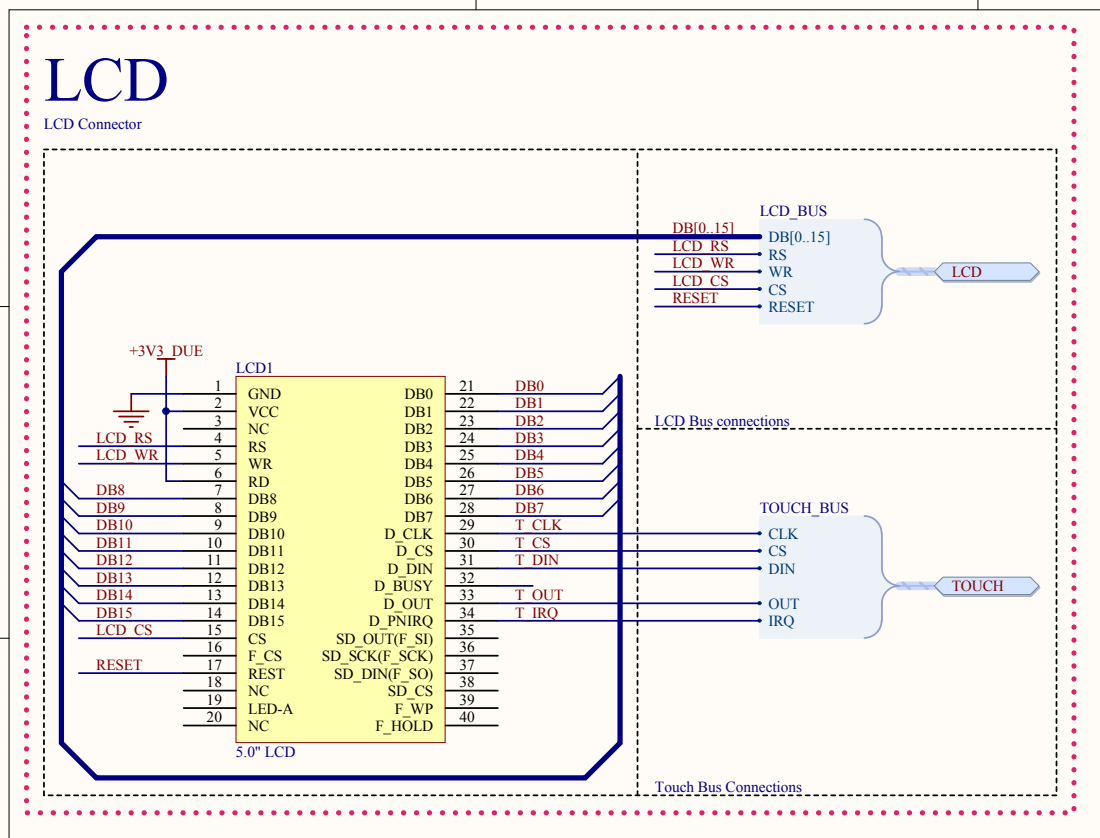
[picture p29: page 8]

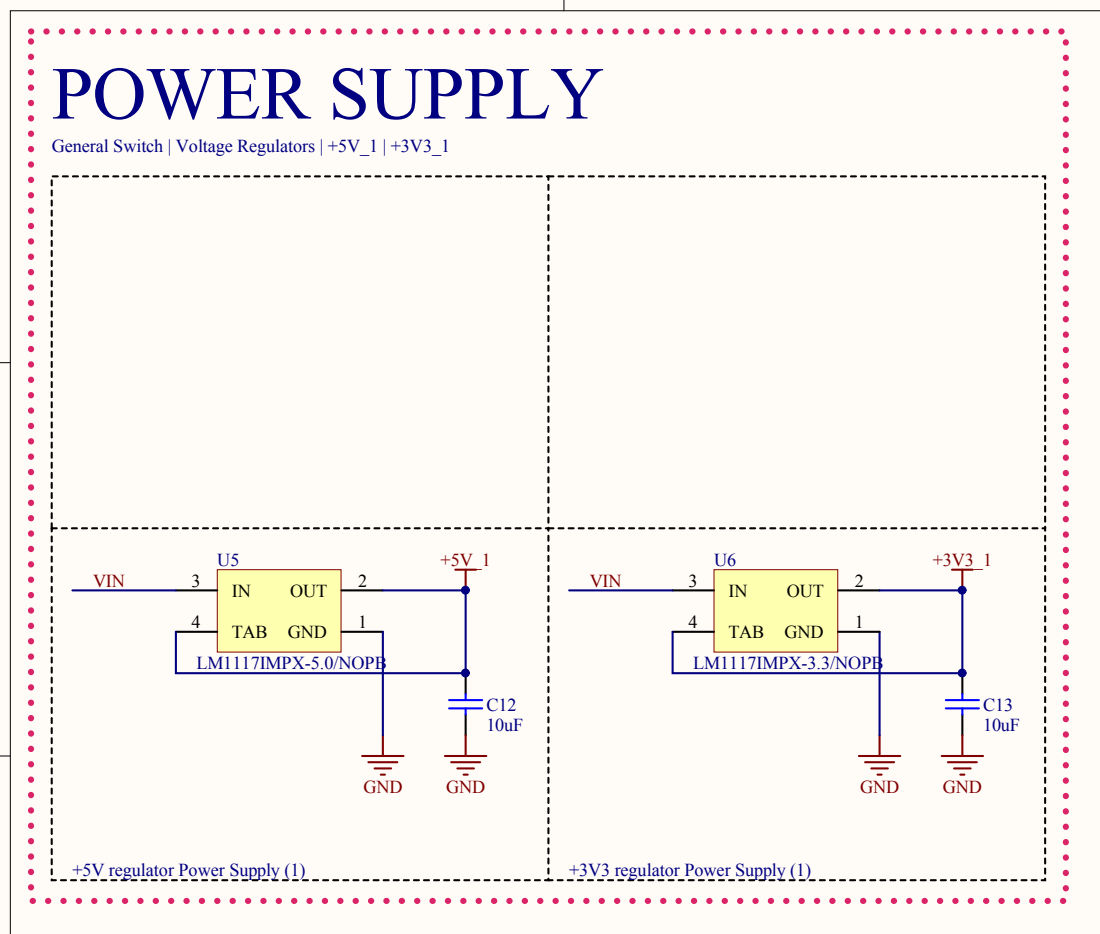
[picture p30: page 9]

POWER SUPPLY General Switch | Voltage Regulators | +5V_1 | +3V3_1

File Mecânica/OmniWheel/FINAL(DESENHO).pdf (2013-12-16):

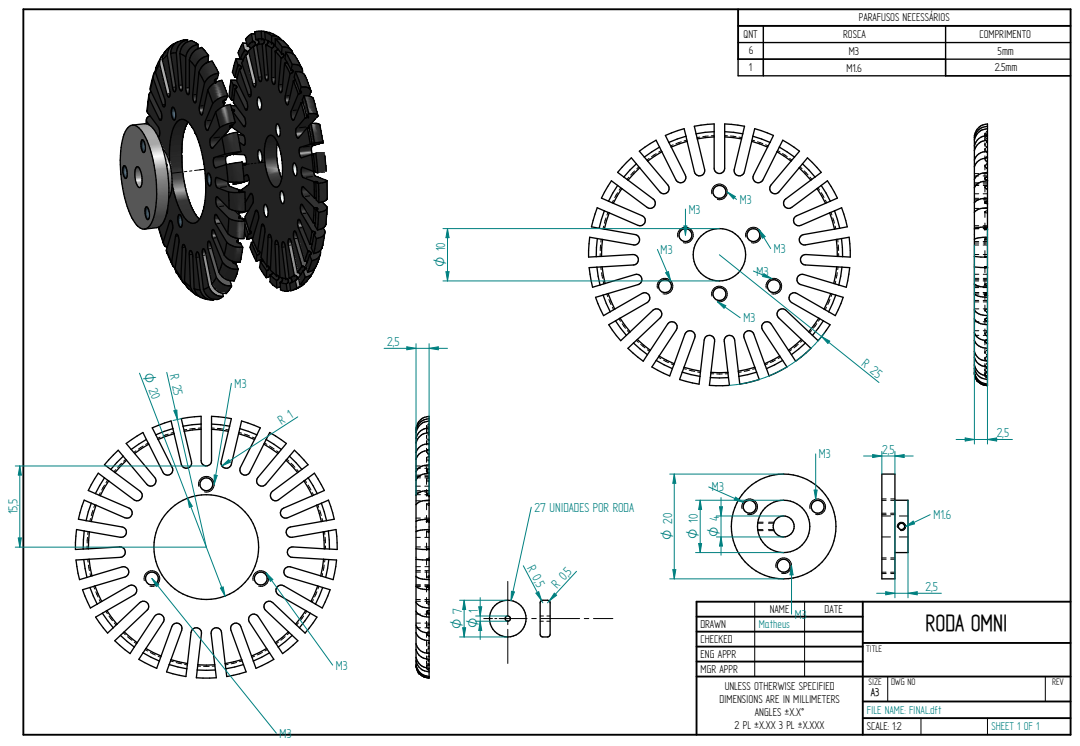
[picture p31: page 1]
TITLE; SCALE: 1:2; SHEET 1 OF 1

PARAFUSOS NECESSÁRIOS

QNT | ROSCA | COMPRIMENTO
6 | M3 | 5mm
1 | M1.6 | 2.5mm

M1.6 27 UNIDADES POR RODA

NAME M3 | DATE | RODA OMNI

DRAWN | Matheus
CHECKED
ENG APPR
MGR APPR
UNLESS OTHERWISE SPECIFIED DIMENSIONS ARE IN MILLIMETERS ANGLES ±X.X° 2 PL ±X.XX 3 PL ±X.XXX | SIZE A3 | DWG NO | REV

FILE NAME: FINAL.dft

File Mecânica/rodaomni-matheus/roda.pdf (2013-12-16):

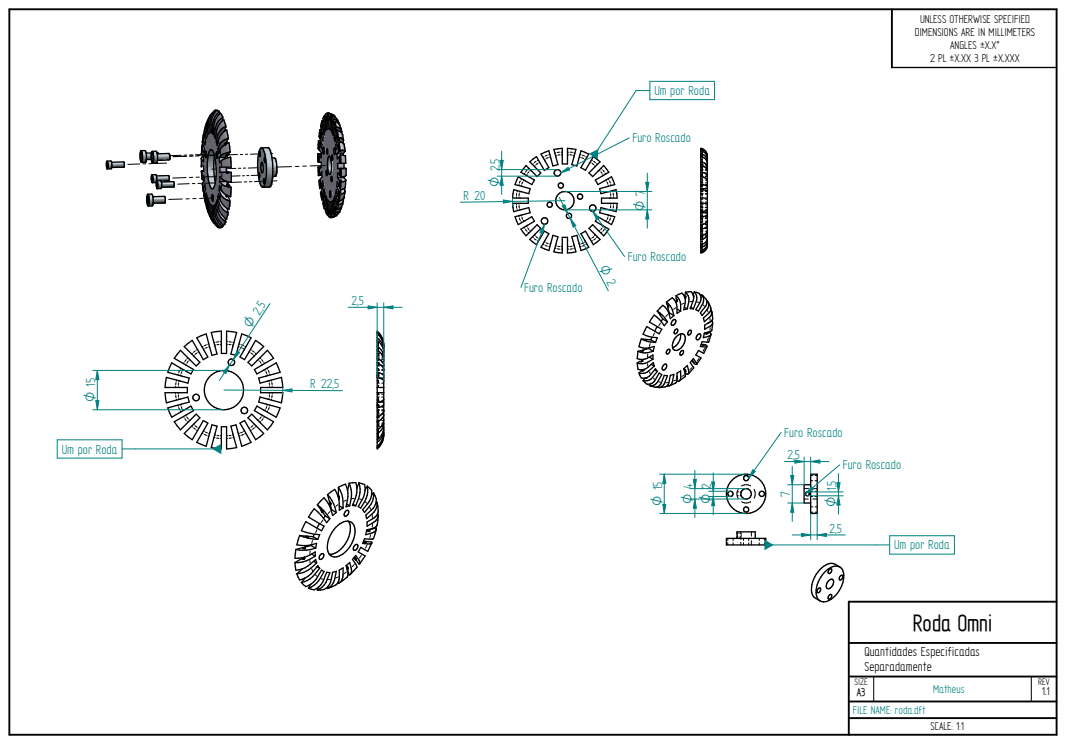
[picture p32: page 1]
Matheus; Roda Omni; REV; SCALE: 1:1; Furo Roscado

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

Um por Roda

Quantidades Especificadas
Separadamente
SIZE
FILE NAME: roda.dft

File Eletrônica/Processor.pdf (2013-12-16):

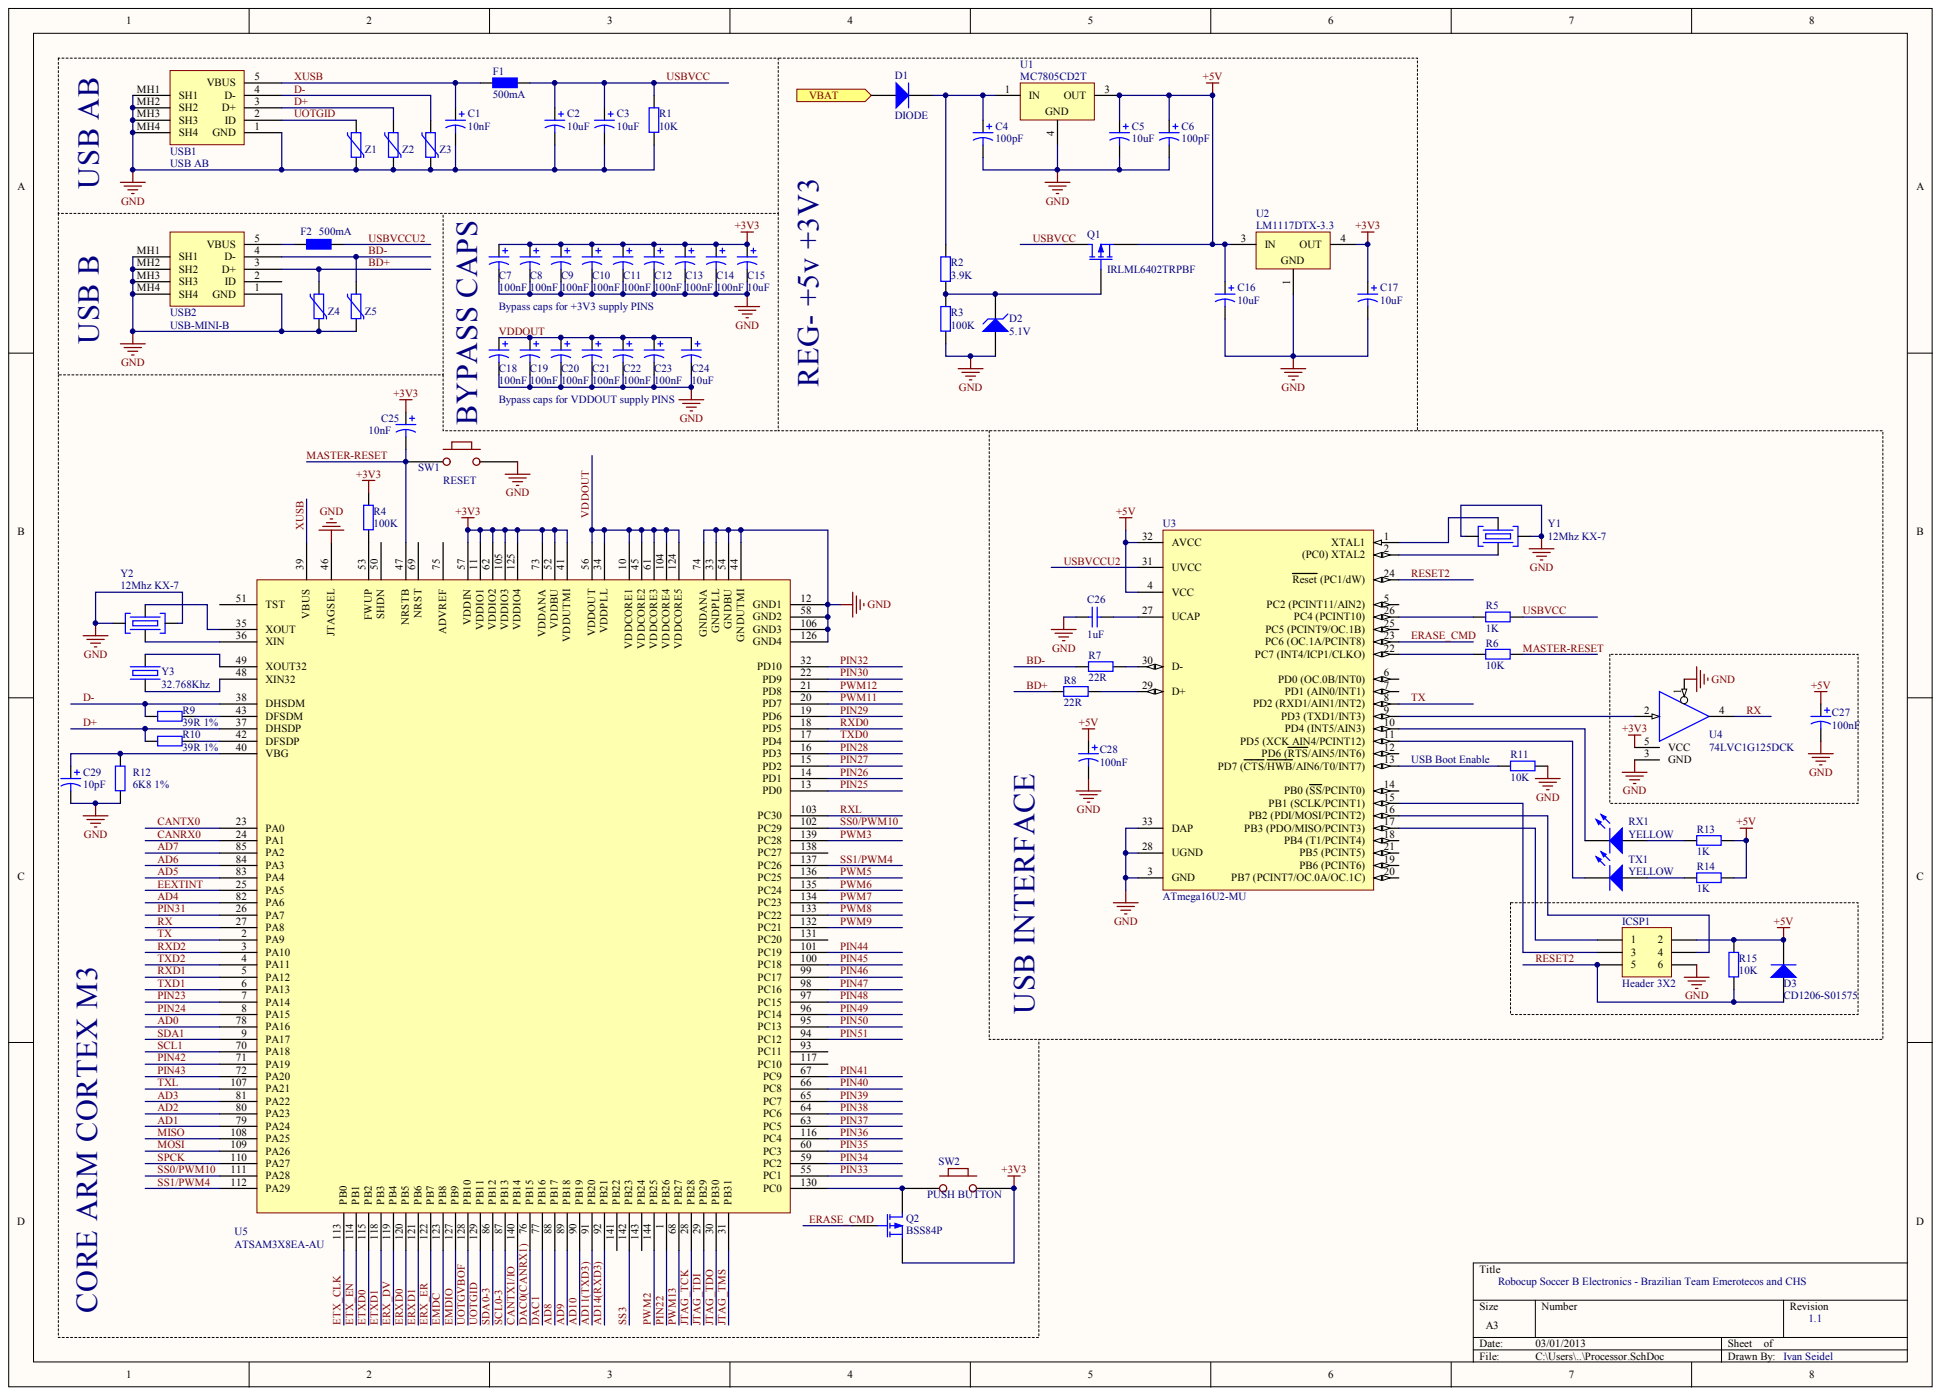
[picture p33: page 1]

Bypass caps for +3V3 supply PINS

Bypass caps for VDDOUT supply PINS

Title
Robocup Soccer B Electronics - Brazilian Team Emerotecos and CHS

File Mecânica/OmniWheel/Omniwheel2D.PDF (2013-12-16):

24 partes - (escala 5:1); Geral (escala 1:1); 2 partes - (escala 5:1); RobotCup 2013 - Soccer; ESCALA: Especificado no desenho; SHEET 1 OF 1; DWG NO.; Emerotecos & CHS

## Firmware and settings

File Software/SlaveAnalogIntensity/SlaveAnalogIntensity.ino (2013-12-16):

#include <inttypes.h>
#include <Arduino.h>

#include "math.h"
#include "ArduinoSensors.h"
#include "LinkedList.h"
#include "Gaussian.h"
#include "GaussianAverage.h"

#define BUSY 	8
#define COMMON 	7
#define ENABLE	6

#define SMASK   0b00111100
#define S0 		2
#define S1 		3
#define S2 		4
#define S3 		5

#define N_INTENSITIES 8

int lastIntensities[N_INTENSITIES];
int currIntensity;
long lastMillis;

long sum[16];

uint8_t AnalogIR_Port[8] = {
	A1,
	A0,
	A6,
	A7,
	A4,
	A2,
	A3,
	A5,
};

uint8_t DigitalIR_Port[16] = {
	0b00000100, // IR 1
	0b00000101, // IR 2
	0b00000110, // IR 3
	0b00000111, // IR 4
	0b00001000, // IR 5
	0b00001001, // IR 6
	0b00001010, // IR 7
	0b00001011, // IR 8
	0b00001100, // IR 9
	0b00001101, // IR 10
	0b00001110, // IR 11
	0b00001111, // IR 12
	0b00000000, // IR 13
	0b00000001, // IR 14
	0b00000010, // IR 15
	0b00000011, // IR 16
};

/*
	Output registers to S0-S3,
	outputing the right sequence
	to connect the "ir" to common

	ir: 0 - 15
*/
void selectDigitalChannel(uint8_t ir){

	PORTD = (PORTD & 0b11000011) | (DigitalIR_Port[ir] << S0);

	// Let changes apply to the COMMON port
	asm("nop\n\t");
	asm("nop\n\t");
}
/*
	Read selected digital channel
*/
bool readDigitalChannel(){
	return PIND & (0x01 << COMMON);
}

void setup(){
	Serial.begin(57600);
	while(!Serial);
	// Serial.println("$: Initialized");

	pinMode(BUSY, OUTPUT);

	pinMode(ENABLE, OUTPUT);
	digitalWrite(ENABLE, LOW);	// Enable HC4067

	pinMode(S0, OUTPUT);
	digitalWrite(S0, LOW);
	pinMode(S1, OUTPUT);
	digitalWrite(S1, LOW);
	pinMode(S2, OUTPUT);
	digitalWrite(S2, LOW);
	pinMode(S3, OUTPUT);
	digitalWrite(S3, LOW);

	pinMode(COMMON, INPUT);
	digitalRead(COMMON);
	
	currIntensity = 0;
}


int loops = 0;
long distance = 0;
long avg = 0;

long IR_DigitalValue[16];
long IR_IntegralValue = 0;

#define IR_LOOPS 		550
#define IR_MIN_INTEGRAL 100
#define IR_MIN_REPEATS	10

void getSums() {
	// Clear actual values
	for(int i = 0; i < 16; i++){
		sum[i] = 0;
	}

	// Busy LED on
	digitalWrite(BUSY, HIGH);

	// For each sensor on the MUX...
	for(int i = 0; i < 16; i++){
		selectDigitalChannel(i);

		// Read IR_LOOPS times
		for(long x = 0; x < IR_LOOPS; x++){
			sum[i] += !readDigitalChannel();
			if(sum[i] >= IR_MIN_INTEGRAL)
				break;
		}

	}
	IR_IntegralValue = 0;

	// Filter values, and send to IR_DigitalValue
	for(int i = 0; i < 16; i++){

		// Don't let go farter than IR_MIN_REPEATS, and below 0
		IR_DigitalValue[i] =
			min(IR_MIN_REPEATS,
				max(IR_DigitalValue[i] + (sum[i] >= IR_MIN_INTEGRAL? 1:-1), 0));

		IR_IntegralValue += IR_DigitalValue[i];
	}
	digitalWrite(BUSY, LOW);
}

long xInt = 0;
long yInt = 0;
int getIntensity() {
	int maxIntensity = 0;
	xInt = 0;
	yInt = 0;
	for(int i = 0; i < 8; i++){
		long tempInt = analogRead(AnalogIR_Port[i]);
		maxIntensity = max(maxIntensity, tempInt);

		xInt += cos(i * M_PI/4.0 - M_PI/2.0) * tempInt;
		yInt += sin(i * M_PI/4.0 - M_PI/2.0) * tempInt;
	}
	return maxIntensity;
}

int getMaxIntensity() {
	int ans = 0;
	for (int i = 0; i < N_INTENSITIES; i++)
		ans = max(ans, lastIntensities[i]);
	return ans;
}

//Returns the index, if any, of the first sensor of a continuous group of size qtt which detects the ball
/*int getDirectionWith(int qtt) {
	for (int i = 0; i < 16; i++) {
		//first and last
		if (!IR_DigitalValue[i] || !IR_DigitalValue[(i + qtt - 1) % 16])
			continue;
		
		int qtt_off = 0;
		for (int j = i; j < i + qtt; j++) {
			if (!IR_DigitalValue[j % 16])
				qtt_off++;
		}
		
		if (qtt_off > 30*qtt/100) //at most x % not detecting
			continue;
			
		//return the middle, multiplying by 2 and creating virtual sensors in each gap
		if (qtt & 1)
			return (2 * (i + (qtt / 2))) % 32;
		else
			return (1 + 2 * (i + (qtt / 2 - 1))) % 32;
	}
	
	return 80;
}*/

#define MAX_SENSORS 16
#define K_ANGLE	0

float _tempAngles[MAX_SENSORS] = {
    K_ANGLE + 0.3927 * 0.5,
    K_ANGLE + 0.3927 * 1.5,
    K_ANGLE + 0.3927 * 2.5,
    K_ANGLE + 0.3927 * 3.5,
    K_ANGLE + 0.3927 * 4.5,
    K_ANGLE + 0.3927 * 5.5,
    K_ANGLE + 0.3927 * 6.5,
    K_ANGLE + 0.3927 * 7.5,
    K_ANGLE + 0.3927 * 8.5,
    K_ANGLE + 0.3927 * 9.5,
    K_ANGLE + 0.3927 * 10.5,
    K_ANGLE + 0.3927 * 11.5,
    K_ANGLE + 0.3927 * 12.5,
    K_ANGLE + 0.3927 * 13.5,
    K_ANGLE + 0.3927 * 14.5,
    K_ANGLE + 0.3927 * 15.5
};

float _tempWeights[MAX_SENSORS] = {
    1.0,
    1.0,
    1.0,
    1.0,
    1.0,
    1.0,
    1.0,
    1.0,
    1.0,
    1.0,
    1.0,
    1.0,
    1.0,
    1.0,
    1.0,
    1.0
};

// Filters
GaussianAverage kalmanIntensity(2);
GaussianAverage kalmanDirectionX(2);
GaussianAverage kalmanDirectionY(2);

void printSums() {
	for (int i = 0; i < 16; i++) {
		Serial.print(IR_DigitalValue[i]);
		Serial.print("\t");
	}
	Serial.println();
}

int noBall = 0;

// #define DEBUG	1
int debugDigital = 0;

void loop(){
	
	// DEBUG
	#ifdef DEBUG
		if(Serial.available()){
			while(Serial.available()) Serial.read();
			debugDigital = (debugDigital+1) % 16;
			Serial.print("\t\tActual: ");
			Serial.println(debugDigital);
		}
	#endif

	// Reads intensity, and saves into a circular buffer
	lastIntensities[currIntensity++] = getIntensity();
	if (currIntensity == N_INTENSITIES)
		currIntensity = 0;

	// Read digital Sensors
	getSums();

	if (millis() - lastMillis >= 50) {

		// Get max intensity from sensors
		int maxRawIntensity = getMaxIntensity();

		// Creates a gaussian object to store the intensity and it's variance
		Gaussian gIntensity = Gaussian(maxRawIntensity);
		gIntensity.variance = 10 + abs(kalmanIntensity.process().variance - maxRawIntensity);
		// gIntensity.variance = gIntensity.mean;

		// Add current value to the Gaussian Filter
		kalmanIntensity.add(gIntensity);

		// DEPRECATED
		// int direction = getDirection();

		// Calculate RAW vector modules for measurements
	    double rawX = 0.0;
	    double rawY = 0.0;

	    // #ifndef DEBUG
		int qttDetecting = 0;
		for(int i = 0; i < MAX_SENSORS; i++){
			// Serial.print(IR_DigitalValue[i]);
			// Serial.print("\t");
			
			if (IR_DigitalValue[i])
				qttDetecting++;

			rawX += (IR_DigitalValue[i]*_tempWeights[i])*sin(_tempAngles[i]);
			rawY += (IR_DigitalValue[i]*_tempWeights[i])*cos(_tempAngles[i]);
		}
		//Serial.println(qttDetecting);

		double rawXAnalog = 0.0;
		double rawYAnalog = 0.0;

		double normalizeAnalog = sqrt(xInt*xInt + yInt*yInt);
		if(normalizeAnalog > 10){
			double rawXAnalog = (double) xInt / normalizeAnalog;
			double rawYAnalog = (double) yInt / normalizeAnalog;
		}

		rawX += rawXAnalog * kalmanIntensity.process().mean * (1.0*2.0);
		rawY += rawYAnalog * kalmanIntensity.process().mean * (1.0*2.0);
	    /*#else
	    	rawX += (IR_DigitalValue[debugDigital]*_tempWeights[debugDigital])*sin(_tempAngles[debugDigital]);
	        rawY += (IR_DigitalValue[debugDigitaül]*_tempWeights[debugDigital])*cos(_tempAngles[debugDigital]);
	    #endif*/

	    // Serial.print("\n");
	    double directionDouble;
	    bool ballNotDetected = false;

	    if(rawY == 0.0 && rawX == 0.0){
	    	// noBall ++;

	    	// Check if ball has not been detected for a long period of time
			if(noBall > 8){
				// Set the flag to true
				ballNotDetected = true;
			}

	    }else{
	    	noBall = 0;

	    	// Actual direction, in Radians
		    directionDouble = (atan2(rawX, rawY));
		    
		    double normalizedX = cos(directionDouble);
		    double normalizedY = sin(directionDouble);

		    kalmanDirectionX.add(
		    	Gaussian(
		    		normalizedX,//));//,
		    		1.0 + abs(100 * (normalizedX - kalmanDirectionX.process().variance)) ));

			kalmanDirectionY.add(
				Gaussian(
					normalizedY,//));//,
					1.0 + abs(100 * (normalizedY - kalmanDirectionY.process().variance)) ));

			// Direction is the current RAW direction, read from sensors
		    // direction = constrain( ((int)( toDegs(directionDouble + M_PI) / 11.25)+16) % 32, 1, 127);
		}
		// Filter vectors and saves current x and y
		double filteredX = kalmanDirectionX.process().mean;
		double filteredY = kalmanDirectionY.process().mean;

		// Filtered Angle data, using pseudo-kalman filter
		// + M_PI is to convert from -180/180 to 0/360
		double finalAngle = toDegs(atan2(filteredY, filteredX) + M_PI);

		// This is the byte that is going to be sent to the 
		uint8_t chunkedAngle = 0xFF;
		if(!ballNotDetected)
			chunkedAngle = (uint8_t)(constrain(finalAngle, 0, 360) / 3);

		// Serial.print(angleFinal);
		// Serial.print("\t");
		// Serial.println(direction);

		int intensity = constrain(map(kalmanIntensity.process().mean, 20, 400, 0, 255), 0, 255);
		//intensity = constrain(20 * qttDetecting, 0, 255);
		
		/*
			Protocol definition:
				* 2 Bytes
				* Bit 0 defines TYPE
				
				Case Bit 0 = 0:
					Message is Direction in degrees, divided by 3;

				Case Bit 0 = 1:
					Message is Intensidty;
		*/
		//Bit to indicate type: 1 -> intensity(force odd), 0 -> direction (left shifted to preserve value)
		uint8_t dirByte = chunkedAngle << 1;
		uint8_t intByte = (ballNotDetected? 0 : intensity) |  1;
		


		//Write as simple messages; secured by least significant bit
		#ifdef DEBUG
			// if(angleFinal != 80)
			Serial.print(ballNotDetected*1);
			Serial.print(" | ");
			Serial.print( chunkedAngle );
			Serial.print("\t| ");
			Serial.print( intensity );
			// Serial.print("\t| ");
			Serial.print("\t| X:");
			Serial.print( rawX );
			Serial.print("\t| Y:");
			Serial.println( rawY );
			// printSums();
		#else
			Serial.write(dirByte);
			Serial.write(intByte);
		#endif

		lastMillis = millis();
	}
}

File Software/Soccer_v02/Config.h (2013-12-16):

#include <Arduino.h>
#include <DueTimer.h>

/*
	ROBOT GENERAL CONFIGURATION
*/

// Timers usage definition, to avoid conflicts
#define TIMER_THREAD1	Timer3		// Timer that will trigger threads on ArduinOS
#define TIMER_TCH		Timer4		// Used for LCD hit tests while moving
#define TIMER_LED		Timer5		// Blinking led, to show that "I'm alive!"


// User Interface (LED's, Buzzer...)
#define pLED_STATUS		8
#define pBTN_PAUSE		3
#define pBTN_SW1		7
#define pBTN_SW2		6

// Buzzer configuration
#define pBUZER			22
#define TIME_BEEP		20
#define TIME_BEEP_H		1 			
#define TIME_BEEP_L		200			

// PC (Just for debugging)
#define PC_USART		Serial
#define PC				Serial 		// To simplify

// Bluetooth
#define BLUETOOTH_USART	Serial
#define BLUETOOTH		Serial
#define BT				Serial

// Motor Driver Controller
#define DRIVER1_USART	Serial1
#define DRIVER2_USART	Serial2

// CO-PROCESSOR (ATMEGA328) with Temperature sensors
#define BALL_USART		Serial3

// LCD
// DB0-DB7:  33-40
// DB8-DB15: 51-44
#define pLCD_RS			41
#define pLCD_WR			42
#define pLCD_CS			43
#define pLCD_RESET		53
#define pLCD_LED		9

#define LCDWidth		799
#define	LCDHeight		479

// TOUCH
#define pTCH_CLK		27
#define pTCH_CS			28
#define pTCH_DIN		29
#define pTCH_OUT		30
#define pTCH_IRQ		31

// IMU
#define IMU_WIRE		Wire1
#define pIMU_SDA		SDA1
#define pIMU_SCL		SCL1
#define pIMU_IRQ		32

// SD Card
// Uses SPI pins, no need for definition
#define pSD_CS			52

// Battery voltage
#define pVIN			A11
#define VOLTAGE_USB		130			// In raw units of analogRead()
#define VOLTAGE_LOW		6.4
#define VOLTAGE_HIGH	8.2

// Temperature Sensor and Cooler definitions
#define pTEMP_SENSOR	A10
#define pTEMP_COOLER	11

// Servo Configuration
#define pSERVO_1		12
#define pSERVO_2		13

// Light sensor pin
#define pLIGHT_SENSOR	A0

// IR and US Distance Sensor
#define pDIST_EN_TOP	4
#define pDIST_EN_BOT	5
#define pDIST_TRIG_TOP	10

#define pDIST_1			A0
#define pDIST_2			A1
#define pDIST_3			A2
#define pDIST_4			A3
#define pDIST_5			A4
#define pDIST_6			A5
#define pDIST_7			A6
#define pDIST_8			A7
#define pDIST_9			A8
#define pDIST_10		A9

int pSENSOR[] = {
	pDIST_1,
	pDIST_2,
	pDIST_3,
	pDIST_4,
	pDIST_5,
	pDIST_6,
	pDIST_7,
	pDIST_8,
	pDIST_9,
	pDIST_10
};

/*
	LCD Schemes
*/
#define cRectFill		200,200,200
#define cTextNeutral	30,30,30
#define cGUITopBarFill	255,255,255

#define fTextBig		OCR_A_Extended_M
#define fTextSmall		SmallFont
#define fNumBig			SevenSegNumFont

/*
	ArduinOS Configuration
*/
#define osRETURN_MIN_TIME	100		// Minimum time between clicks on return Btn
									// to debounce sensor. (in Milliseconds)
									
#define UPDATE_GUI_INTERVAL	2000	// Time to update GUI (constantly)
									// Also compute the remaining battery

#define fGUI_USB			9

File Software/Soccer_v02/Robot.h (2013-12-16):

#include <Arduino.h>

// Motors incluedes
#include "PololuDriver.h"
#include "MoveController.h"
// #include "mbed_driver.h"

// General peripheral includes
// #include <DueTimer.h>
// #include <UTouch.h>
// #include <UTFT.h>

// Operational System
// #include <ArduinOS.h>

// Include Icons and fonts
// #include <fGUI.c>

/*
	GLOBAL Sensors objects
*/
// IMU setup
#ifndef DISABLE_IMU
	MPUSensor *IMU;
#endif

// SENSORS setup
#ifndef DISABLE_SENSORS
	HMC6352 *Compass;

	DistanceInterface 	*Dist[4];
	
	AnalogIn			*analogPins[4];
	bool				lineEnabled[4] = { true, false, false, false };

	DistanceInterface 	*DistLeft,
						*DistRight,
						*DistFront,
						*DistBack;

	LightSensor			*LineSensor;

	BallRadar			*Ball;
#endif

/*
    MoveController definitions
*/
#ifndef DISABLE_MOTION
	PololuDriver *MD;
	MoveController *MC;
#endif

/*
	LED Status timer interrupt
*/
/*void irqLedStatus(){
	static bool active = false;

	 PIO_SetOutput( g_APinDescription[pLED_STATUS].pPort, g_APinDescription[pLED_STATUS].ulPin, active, 0, PIO_PULLUP ) ;
}*/

/*
	RETURN Button implementation
*/
void irqReturnBtn(){
	// Serial.println("PRESS!");
	static long lastCall = 0;
	// Check if there was a minimum time between clicks (debounce)
	if(millis()- lastCall < osRETURN_MIN_TIME)
		return;

	lastCall = millis();
	ArduinOS::actionHandler(ACTION_RETURN);
}

void irqPauseBtn(){
	bool pause = !digitalRead(pBTN_PAUSE);

	Activity* act = ActivityManager::getCurrentActivity();
	if(!act || !act->enablePause())
		return;
	
	// Serial.println(pause ? "Pausing..." : "Continuing...");
    
    if(pause)
        act->pause();
    else
        act->resume();

	delayMicroseconds(10);
}

/*
	Beep function and Thread
*/
// Used to warn battery
Thread thrBeeper;
void onBeeper(){
	static bool beeping = false;
	beeping = !beeping;
	digitalWrite(pBUZER, beeping);
	if(beeping)
		thrBeeper.setInterval(TIME_BEEP_H);
	else
		thrBeeper.setInterval(TIME_BEEP_L);
}

// Notify touchs
void beep(int n = 1){
	digitalWrite(pBUZER, HIGH);
	delayMicroseconds(10000);
	digitalWrite(pBUZER, LOW);

	if(n <= 1)
		return;

	for(int i = 1; i < n; i++){
		delayMicroseconds(6000);
		digitalWrite(pBUZER, HIGH);
		delayMicroseconds(10000);
		digitalWrite(pBUZER, LOW);
	}
}


#ifndef DISABLE_LCD
	/*
		LCD and Touch definitions
	*/
	UTFT LCD(ITDB50,pLCD_RS,pLCD_WR,pLCD_CS,pLCD_RESET);
	UTouch TCH = UTouch(pTCH_CLK,pTCH_CS,pTCH_DIN,pTCH_OUT,pTCH_IRQ);

	// extern uint8_t SmallFont[];			// Font
	// extern uint8_t BigFont[];		// Font
	extern uint8_t OCR_A_Extended_M[];	// Font
	// extern uint8_t SevenSegNumFont[];	// Font
	extern uint8_t fGUI[];				// Font


	/*
		System GUI (General User Interface)
	*/
	Thread thrUpdateGUI;
	View GUI = View();
	void onGUIupdate(){
		static float voltage, analog;
		static int batteryStatus, failsCount = 0;
		LCD.setBackColor(cGUITopBarFill);
		
		// Print BT status
		LCD.setFont(fGUI);
		LCD.setColor(180,180,180);
		LCD.printNumI(6, 1,1);
		

		// Calculates battery voltage and current status
		analog = analogRead(pVIN);
		voltage = max((analog-175)/86.25 + 5.3, 0);

		if(analog <= VOLTAGE_USB){
			batteryStatus = fGUI_USB;	// On USB
		}else{
			batteryStatus = 
				max(0,min(5,map(voltage*100, VOLTAGE_LOW*100, VOLTAGE_HIGH*100,
					0,5)));
		}

		if(batteryStatus == 0){
			if(++failsCount >= 3)
				thrBeeper.enabled = true;	// Enable Beeper thread
			LCD.setColor(240,20,30);	// Very low
		}else if(batteryStatus == fGUI_USB){
			LCD.setColor(70,70,70);		// USB Plugged
		}else if(batteryStatus >=  4){
			LCD.setColor(20,200,20);	// Full charge
		}else{
			LCD.setColor(245,210,95);	// Normal
		}

		if(batteryStatus != 0){
			thrBeeper.enabled = false;	// Disable Beeper thread
			digitalWrite(pBUZER, LOW); 	// Stop beeping
			failsCount = 0;
		}

		// Render Battery status
		LCD.printNumI(batteryStatus, 731,1);
		LCD.setFont(fTextBig);
		LCD.setColor(150,150,150);
		if(batteryStatus != fGUI_USB)
			LCD.printNumF(voltage,1, 665,4,'.',4);
		else
			LCD.print("USB",680,4);

		LCD.print(String(ArduinOS::cpuThreadUsage) + "%  ", 78,4);
	}
	
	void onGUIrender(){
		static Activity* act;
		act = ActivityManager::getCurrentActivity();

		LCD.setColor(cGUITopBarFill);
		LCD.fillRect(0,0,LCDWidth, 31);
		LCD.setBackColor(cGUITopBarFill);

		// Render Activity Name
		if(act){
			LCD.setColor(VGA_BLACK);
			LCD.setFont(fTextBig);
			LCD.print(act->ActivityName, CENTER, 4);
		}

		onGUIupdate();
		// PC.println("$: GUI: Rendered.");
	}

	View STAGE = View();
	void onSTAGErender(){
		LCD.setColor(VGA_BLACK);
		LCD.fillRect(ArduinOS::_rel.x,ArduinOS::_rel.y,LCDWidth, LCDHeight);
	}

	void onInvalidateView(){
		ArduinOS::requestRender = true;
	}

#endif	// DISABLE_LCD

ProgressBar preLoader = ProgressBar();
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

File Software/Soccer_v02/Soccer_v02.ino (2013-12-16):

// ------ ECONOMIZE MEMORY and PROGRAM -------
// Disable Definitions (Make code lighter)

// #define DISABLE_ZYGOTE	1

// #define DISABLE_VICTIM	1
// #define DISABLE_SENSORS	1
#define DISABLE_IMU		1
// #define DISABLE_MOTION	1
// #define DISABLE_LCD		1 	// Also disables Touch
								// Disabling LCD will cause WEIRD things
// --------------------------------------------


// Motors incluedes
#ifndef DISABLE_MOTION
	/*#include "MoveController.h"
	#include ".h"*/ // Driver include
#endif

// General peripheral includes
#include <DueTimer.h>

#include <ArdUI.h>
#include <View.h>

// LCD stuff
#ifndef DISABLE_LCD
	#include <UTouch.h>
	#include <UTFT.h>
#endif

//#include "Util.h"

// IMU includes
#include <Wire.h>
#ifndef DISABLE_IMU
	#include "Wire.h"
	#include "I2Cdev.h"
	#include "dmpMPU9150.h"
	#include "sensors/MPUSensor.h"
#endif

#ifndef DISABLE_ZYGOTE
	#include <LinkedList.h>
#endif

// Sensors
#include <AnalogIn.h>
#include <DigitalIn.h>
#include <sensors/SharpLong.h>
#include <sensors/SharpLong.h>
#include <sensors/EZUltrasonicAnalog.h>
#include <sensors/HMC6352.h>
#include "LightSensor.h"
#include <BallRadar.h>

// Operational System
#include <Thread.h>
#include <ArduinOS.h>
#include <views/Button.h>
#include <views/CheckBox.h>
#include <views/SeekBar.h>
#include <views/TextView.h>
#include <views/AngleView.h>
#include <ArduinoSensors.h>

//Motors
#include "MoveDriver.h"
#include "MoveController.h"
#include "PololuDriver.h"

// Basic robot definitions
#include "Config.h"
#include "Robot.h"

//Utility classes
#include <Gaussian.h>
#include <GaussianAverage.h>

#include "CompassPID.h"

// Activity includes
#include "MainActivity.h"
#include "TestMotorsActivity.h"
#include "TestUltrasonicActivity.h"
#include "TestBallSensorsActivity.h"
#include "TestCompassActivity.h"
#include "CalibrateActivity.h"
#include "TestLineDetectionActivity.h"
#include "TestBrakesActivity.h";
#include "ChaseBallActivity.h"
#include "ForwardActivity.h"
#include "GoalkeeperActivity.h"

#ifndef DISABLE_IMU
	#include "TestIMUActivity.h"
#endif

#ifndef DISABLE_ZYGOTE
	MainActivity zygote = MainActivity();
#endif

Button back = Button();

char c;
void serial(){

	/*if(PC.available() > 0){
		c = PC.read();

		if(!c)
		return;

        // Serial.print("$ thread: got: ");
        // Serial.println(c);
        Activity* act = ActivityManager::getCurrentActivity();
        if(c == 'p'){
            // Serial.print("$ Thread: pausing Activity: ");
            // Serial.println(act->ActivityID);
            act->pause();
            }else if(c == 'r'){
            // Serial.print("$ Thread: resuming Activity: ");
            // Serial.println(act->ActivityID);
            act->resume();
            }else if(c == 's'){
            // Serial.print("$ Thread: resuming Activity: ");
            // Serial.println(act->ActivityID);
            act->stop();
            }else if(c == 'k'){
            // Serial.print("$ Thread: resuming Activity: ");
            // Serial.println(act->ActivityID);
            act->kill();
            }else if(c == 'g'){
            	PC.print("$ Thread: Current Activity: ");
            	PC.println(act->ActivityID);
            // act->kill();
        }
    }*/

    // if(PC.available()){
    // 	Serial.println();

	   //  while(PC.available() > 0)
	   //  	PC.print(PC.read());
	    	
    // 	Serial.println();
    // }

    // if(BT.available() > 0){
    // 	PC.write(BT.read());
    // }
}

void goBack(){
	beep();
	ActivityManager::getCurrentActivity()->stop();
}

void setup(){
	initRobot();

	// Timer.getAvailable().attachInterrupt(serial).start(50);
	
	ChaseBallActivity *chaseBallAct = new ChaseBallActivity(MC, Ball);
	TestMotorsActivity *testMotorsAct = new TestMotorsActivity(MC);
	TestUltrasonicActivity *testUltrasonicAct = new TestUltrasonicActivity();
	TestBallSensorsActivity *testBallSensorsAct = new TestBallSensorsActivity();
	TestCompassActivity *testCompassAct = new TestCompassActivity();
	TestLineDetectionActivity *testLineAct = new TestLineDetectionActivity(lineEnabled, MC);
	TestBrakesActivity *testBrakesAct = new TestBrakesActivity(MC);
	ForwardActivity *forwardAct = new ForwardActivity(MC);
	GoalkeeperActivity *goalkeeperAct = new GoalkeeperActivity(MC);
	#ifndef DISABLE_IMU
		TestIMUActivity *testIMUAct = new TestIMUActivity();
	#endif

	#ifndef DISABLE_ZYGOTE

		zygote.activities->add(chaseBallAct);
		zygote.activities->add(testMotorsAct);
		zygote.activities->add(testUltrasonicAct);
		zygote.activities->add(testBallSensorsAct);
		zygote.activities->add(testCompassAct);
		zygote.activities->add(testLineAct);
		zygote.activities->add(testBrakesAct);
		zygote.activities->add(forwardAct);
		zygote.activities->add(goalkeeperAct);

		#ifndef DISABLE_IMU
			zygote.activities->add(testIMUAct);
		#endif
	
		zygote.o.x = 5;
		zygote.o.y = 5;
		zygote.initialize();
	#endif

	back.setArea(640,400,150,40);
	back.name = String("Return");
	back.onClick(goBack);

	chaseBallAct->addView(&back);
	testMotorsAct->addView(&back);
	testUltrasonicAct->addView(&back);
	testBallSensorsAct->addView(&back);
	testBrakesAct->addView(&back);
	forwardAct->addView(&back);
	goalkeeperAct->addView(&back);
	//testCompassAct->addView(&back);
	
	#ifndef DISABLE_IMU
		testIMUAct->addView(&back);
	#endif
}

void loop(){
	PC.println("====== START OF PROGRAM ======");
    // Start Activity
    #ifndef DISABLE_ZYGOTE
    	zygote.start();
    #else
    	// Enter code here to run "custom" zygote
	#endif
    // End of Program
    PC.println("====== END OF PROGRAM ======");
}

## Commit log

2013-12-16 Electronics upload
    [367500304.sldasm, Analog Ball Sensor.SchDoc, Arduino DUE.PcbDoc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]
2013-12-16 Mechanics upload
    [367520784.sldasm, 367523728.sldasm, 408527984.sldasm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]
2013-12-16 Midia files
    Infographics, renders, tshirts, banners, photos and sketches
    [Planilha de custos-Soccer.xlsx]
